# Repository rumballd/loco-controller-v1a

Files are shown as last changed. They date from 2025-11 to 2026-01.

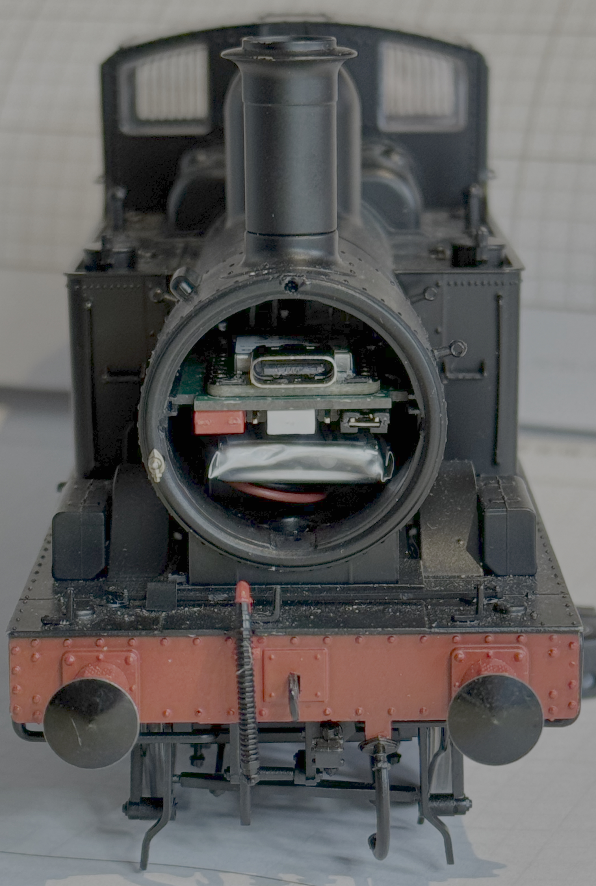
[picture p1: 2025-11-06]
docs/images/fitted_in_14XX.jpg

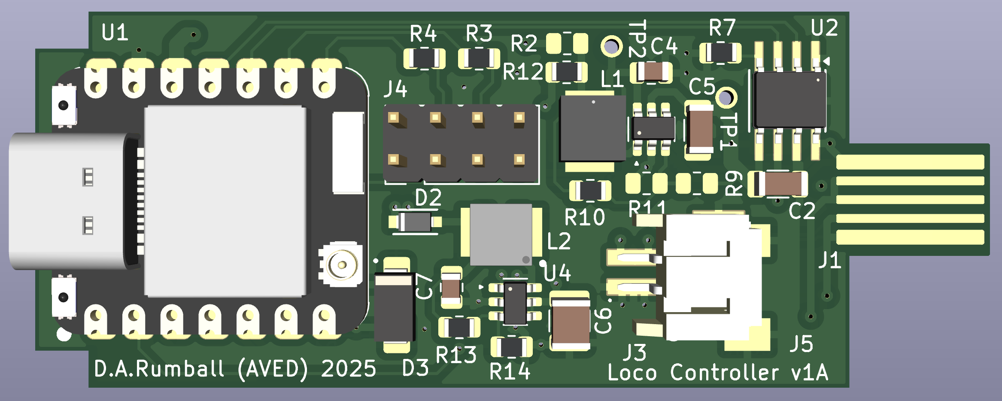
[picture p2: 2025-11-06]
docs/images/top view.png

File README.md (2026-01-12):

# loco-controller-v1a

NEW - Jan 2026, additional firmware examples and Handheld controller firmware

The Loco Controller is designed to offer a simple upgrade of Dapol and other locomotives to battery power and wireless control. It is highly integrated, incorporating an ESP32-C6 dual core MCU (microcontroller Unit) module together with a motor driver, voltage booster, battery charger and input power conditioner all on a single double sided PCB. 

The controller is designed as an exact replacement for the factory fitted DCC decoder adaptor installed in newer Dapol locomotives and installation consists of sliding out the factory PCB and replacing it with the controller. On the 58XX and B4 models the battery also slides in underneath the controller and is connected directly to the controller PCB.

For non Dapol locomotives there are a range of signals and power sources available on 2.54mm spacing pin headers including motor drive and LED outputs. In these cases though some disassembly of the locomotive body and soldering will be required.

Although designed primarily as a controller for motorised devices the device can also function as a generic wireless interface for signals, turnouts and other accessories. In such a ‘fixed’ application the unit can operate without a connected battery being powered solely by externally connected power sources and can drive multiple LED or servo outputs.

The controller implements a Wi-Fi access point and Web server that serves a page of locomotive specific controls to any standard web browser on a phone or tablet 

The initial hardware and firmware release supports:-

• Connector compatible with Dapol 0 Gauge 58XX and B4 locomotives

• Aux connector for other models with power, motor, LED and servo drive

• Integral voltage boost from VBAT to 12 V for the motor at 1 A

• Integral battery charger with power in via track or USB and 2mm JST socket for a 1S Li-Po battery

• Track power input is compatible with DCC and can be up to +-50 VDC with protection against inductive
 spikes
• Battery voltage and USB voltage can be monitored in firmware

• Links provided to isolate track power and the battery

• Charging is indicated by firebox LEDs in Dapol models and also in UI

• Multiple levels of over-current/over-voltage/over-temperature protection

• Integral Wi-Fi access point and Web server

• Control by standard Web browsers (up to four simultaneous connections)

• Firmware is updatable via USB connection

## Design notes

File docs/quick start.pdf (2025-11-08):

Loco Controller Quick Start Guide | Version 0.90 Oct 2025

### Loco Controller ‘Quick Start’ guide

Introduction

This guide gives a quick overview of choosing a battery, installation of the Loco Controller in Dapol and non Dapol models and the operation of the default firmware. There is more detail in the User Notes and other documentation.

Please read Appendix 1 of the User Notes for more information on battery care and safety.

### Battery Selection

Since the choice of battery is dependent on the particulars of the installation a battery is not provided with the unit.

The controller is designed to work only with a 1S Lithium-Polymer (Li-Po) cell with a 2 mm JST-style connector.

WARNING – Battery fire or injury. If the battery cannot supply 1 A continuous or lacks internal protection, it can overheat, ignite, or fail. Use a protected 1S Li-Po rated ≥1 A continuous from a reputable

An example of a suitable battery is the LP602248 from EEMB. (https://www.amazon.co.uk/EEMB-Battery-Rechargeable-Connector-Certified/dp/B095VVR4LB?th=1)

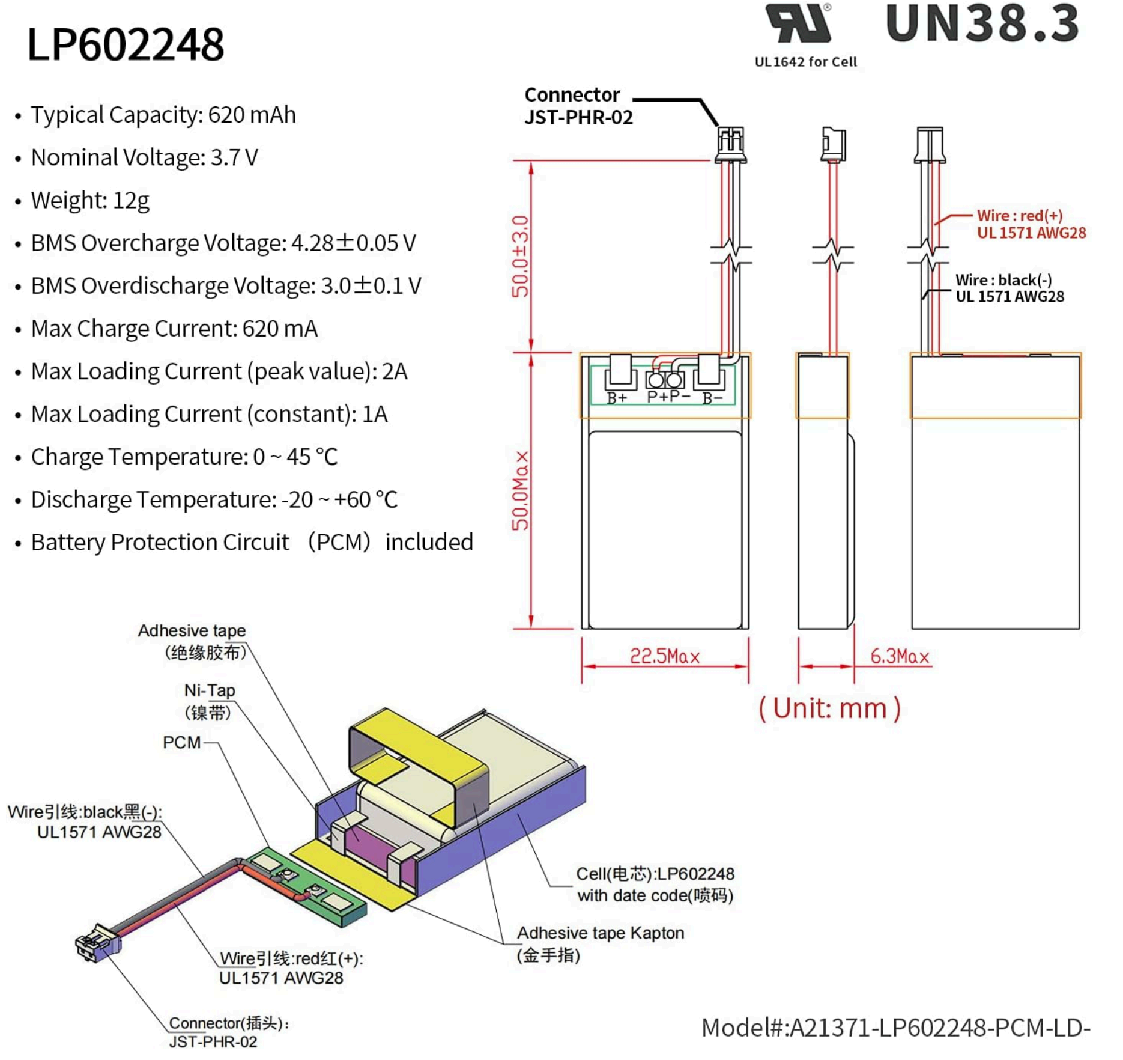
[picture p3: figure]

### Connections

The PCB has five main connectors, a USB-C socket that can be used for charging and loading firmware, the Li-Po battery connector, an ‘edge’ style connector that plugs into a Dapol locomotive’s 10 pin internal socket, a set of 2.54 mm header pins under the front of the PCB with options for powering the device and a 2.54 mm header auxiliary connector that provides access to internal power, motor, LED and servo drive in models that don’t use the Dapol connector.

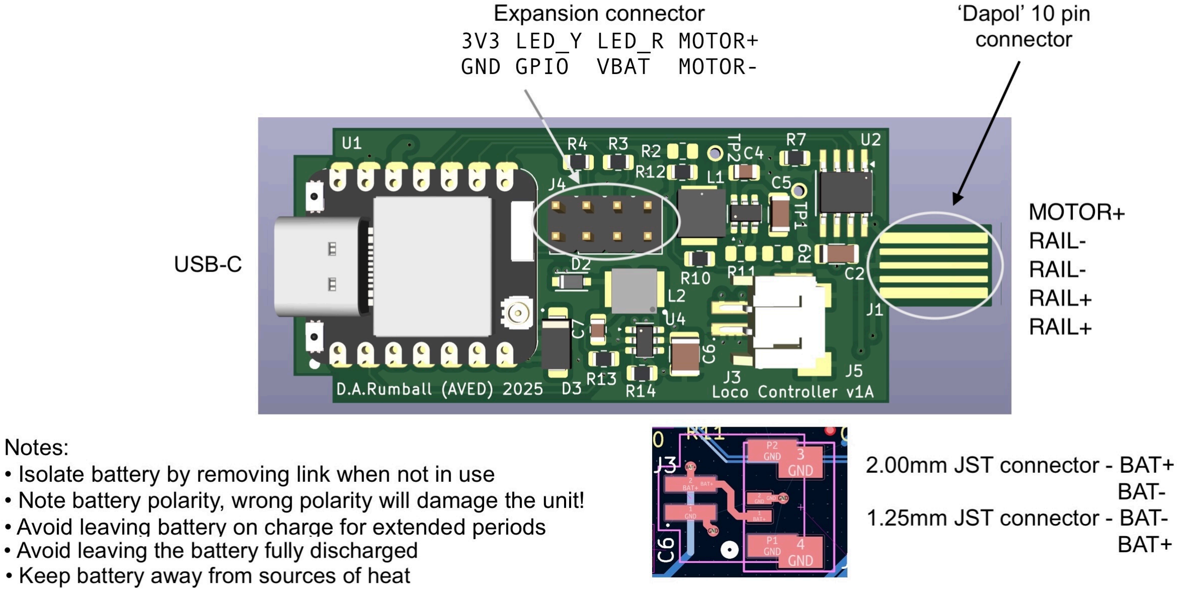
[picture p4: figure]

The battery is connected via a standard JST-style 2mm connector.

CAUTION – Equipment damage. The PCB has no reverse-polarity protection. Confirm battery polarity before you connect the battery.

The battery negative is connected to GND on the PCB and the connection diagram above shows the polarity of the battery connector.

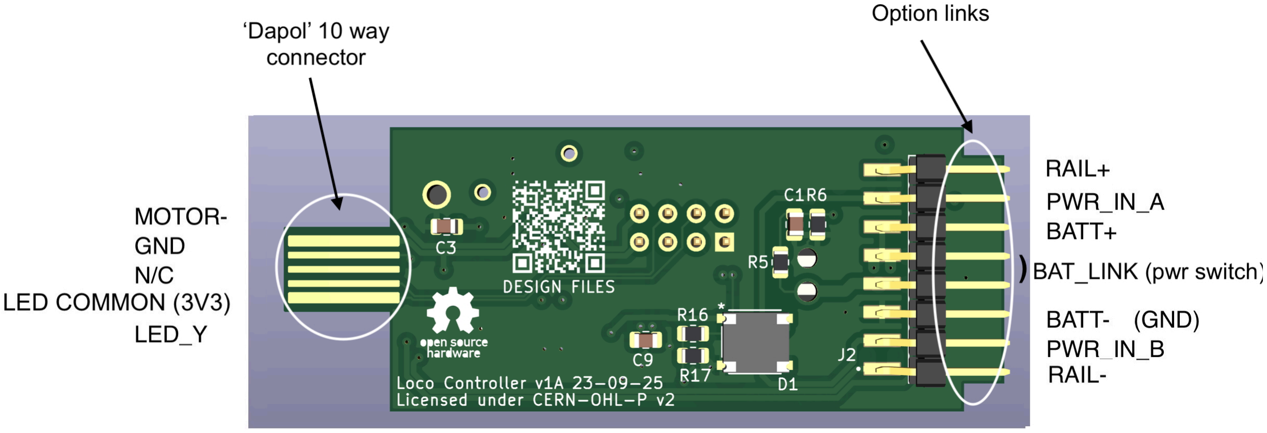
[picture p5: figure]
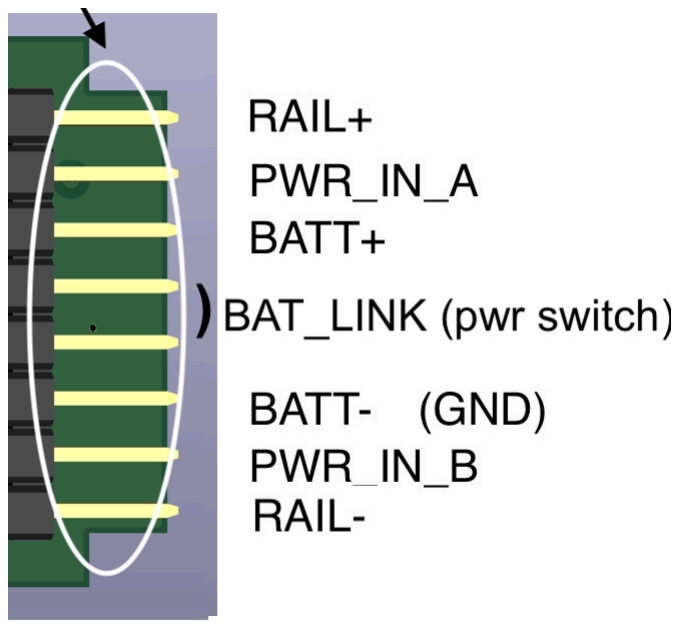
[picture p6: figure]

The links at the front of the PCB allow for the isolation of the battery which can be used as a power switch (or alternatively used for connecting an external switch) and provide for the isolation of external track power by removing the two outer links. When these links are removed the battery can still be charged via the USB-C connector and external power can be supplied through the front header pins.

### Status LEDs

There are two LEDs on the ESP32 module which are visible from the front if the smokebox door is open. Viewed from the front on the left hand side is a yellow flashing LED that indicates normal operation of the firmware and on the right hand side is a red LED that indicates charging status :-

- When no battery is connected:
- The red light turns on when the Type-C cable is connected and turns off after 30 seconds.
- When a battery is connected and the Type-C cable is plugged in for charging:
- The red light flashes.
- When the battery is fully charged via the Type-C connection:
- The red light turns off.

### Battery Charging

The controller has an on board charger which provides a maximum battery charge current of approximately 100 mA, a limit set for thermal dissipation reasons in the charger and to provide safe charging for low capacity cells. The charger is designed for Li-Po cells with high-precision linear constant-current and constant-voltage charging. It can automatically complete the processes of pre-charge, fast-charge, trickle floating charge, voltage fold-back holding, resistive voltage drop compensation and recharge. For more information please see the SGM40567 data sheet included as part of the documentation.

The supply for the charger can be either via the USB-C connector
(500 mA @ 5 V) or via the connections for external power. External power can be between 12 V and 50 VDC, is protected from inductive spikes above 54 V and is insensitive to polarity. The current draw will depend on the applied voltage. The buck regulator used in the power conditioning stage has a maximum input voltage of 70 V which is well above the TVS clipping voltage of approx 55 V.

The controller can switch seamlessly between internal battery power and external charging without operator intervention. Do not apply external power and USB power at the same time.

With the current firmware the firebox LEDs of the 58XX and B4 locomotives will illuminate if external charging power is detected providing an easy way to check on charging status from outside the locomotive. Additionally the User Interface (UI) will show a ‘charging’ indicator although note that this is an indicator of external power rather than the actual charging status. However the battery voltage can be used to estimate the actual state of charge.

### Battery Care

Please read Appendix 1 of the User Notes for more information on battery care and safety.

For long life, do not store Li-Po batteries fully charged or fully discharged. Store at about 50% state of charge (3.8 V).” Always isolate the battery after use either with an external power switch or by the battery link at the front of the PCB to avoid the Microcontroller Unit (MCU) completely draining the battery.

Although in normal operation the battery should not itself get hot, care should be taken in the location of the battery to keep it away from any heat sources. On the controller PCB these are located on the top side but as heat sinking is provided by the inner layers of the PCB the controller can become warm with use.

Care should also be taken to avoid compressing or bending the battery during installation as this will damage the cell.

Check your batteries regularly for any signs of damage, leakage or swelling of the cell. If you notice any issues then the battery should be disposed of safely. Do not dispose in your normal waste but rather take it to a recycling centre for safe disposal.

Installation in Dapol models with the internal 10 pin connector

This installation method has been tested with the current versions of the Dapol 14/58XX and B4 models which are fitted with a 10 way card edge connector. There may be other compatible models in the future but you should check that the connector pin out is the same before installation.

The installation process itself is simple. First open the smokebox door and remove the factory fitted DCC decoder carrier PCB then replace this with the loco controller and battery. Check that the PCB slides in without any force required, the battery is a loose fit and clear of the underneath of the controller PCB and the battery or it’s connecting wire aren’t fouling any parts of the locomotive. Check that the links are set as desired and the ‘alive’ yellow LED is flashing.

That’s it! You can now connect to the controller’s WiFi access point as described in the ‘Operation’ section below.

Installation in other models

As the installation in other locomotives will be varied it’s not possible to give exact instructions but instead here are some general hints and tips:-

- If not using the ‘Dapol’ connector insulate it with a wrap of tape or heat shrink.
- All the required signals and power for a typical installation should be available on the link and expansion header pins.
- ALWAYS arrange for the battery to be isolated via a power switch connected to the battery link pins.
- If there are metal parts in the vicinity of the controller it may be necessary to insulate the bottom of the PCB.
- The controller should not get hot during normal operation but air should be allowed to circulate around the PCB to remove any generated heat.
- Take great care with positioning and installation of the battery, it should not be exposed to any sources of heat or subjected to mechanical bending or pressure.

Operation

The default firmware that is shipped with the controller gives a semi realistic set of controls implementing a very simple (and not quite correct) ‘physics’ model that simulates the characteristics of a steam locomotive including momentum and friction etc.

The firmware instantiates a 2.4 GHz Wi-Fi access point capable of supporting four simultaneous connections together with a simple Web server appearing on port 80. This server provides a page defined by files stored in the ESP32’s flash based file system.

To use the controller connect your device’s Wi-Fi to the locomotives AP, which defaults to ‘LocoController’. Once connected open a browser and navigate to the IP address 192.168.4.1 then a page of controls will appear in the browser

The current interface offers three sliders
which provide a simple emulation of a steam
locomotive’s controls. To startup set the Reverser to 50% and with the brake off advance the regulator to about 33% and after a short delay the locomotive should move. The firmware implements a very simple ‘physics’ model that takes account of momentum and friction such that if the regulator is shut off the locomotive will coast, gradually slowing down. Applying the brake will increase friction thus increasing the rate of slowing. To reverse repeat the above but set the reverser to -50%

To emulate a traditional ‘direct’ controller first set the regulator to 100% after which the reverser will act as an analogue control directly
setting the locomotive speed.

As an aid to judging the charge state of the battery

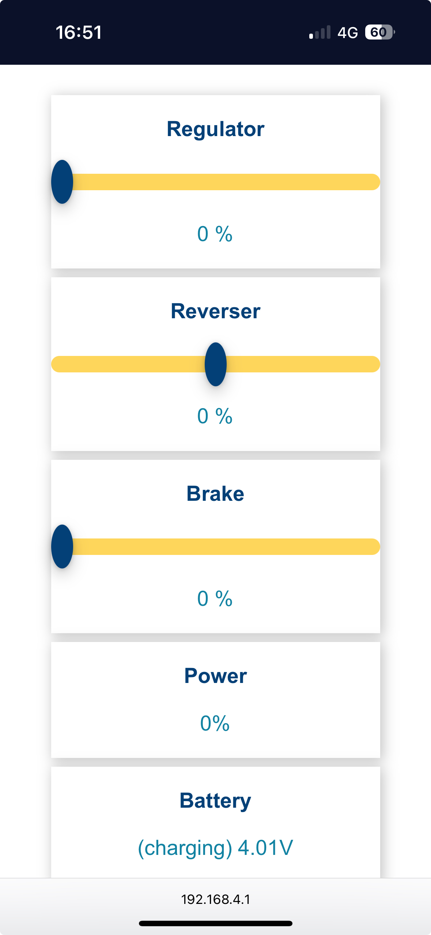
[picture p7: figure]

the battery voltage is displayed. Empty corresponds to approx 3.5 V and full 4.1 V. When track power is detected then the battery voltage will be prepended with a ‘charging’ message. Note that this is a proxy for the battery charging state as it isn’t directly possible to sense charging.

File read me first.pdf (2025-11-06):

Version 0.90 1st Oct 2025

### Loco Controller distribution 0.90 Oct 2025

This package should contain the following folders :-

* docs | - user notes, quick start and other guides.
* firmware | - Example ESP32-C6 firmware.
* hardware | - PCB fabrication files and component data sheets.

History
2025-10 | ver 0.90 | First release to the outside world.

Known Issues
None

Todo List
None

## WARNING: Please take note of the information and warnings about the use of Li-Po batteries in Appendix 1 of the

User Notes.

This project does not contain polished or shipping quality code or hardware, so use entirely at you own risk.

The project is covered under the permissive version of the CERN Open Hardware Licence Version 2 a copy of which is part of the package.

If you have any problems with the build, find any bugs, have suggestions for features and improvements etc, please email me at lococontroller@aved.org.uk

Above all, Have Fun!

David Rumball
Constantine, UK.

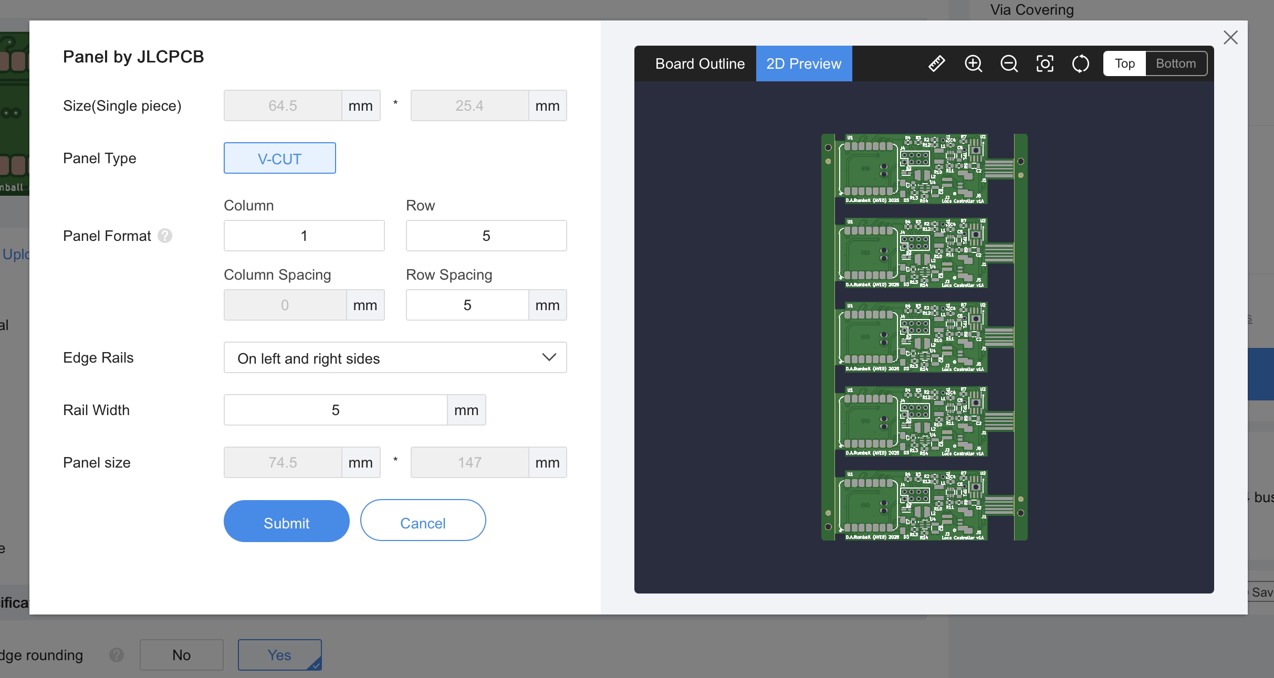
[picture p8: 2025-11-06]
hardware/PCB/fab/1x5 panel layout.jpg

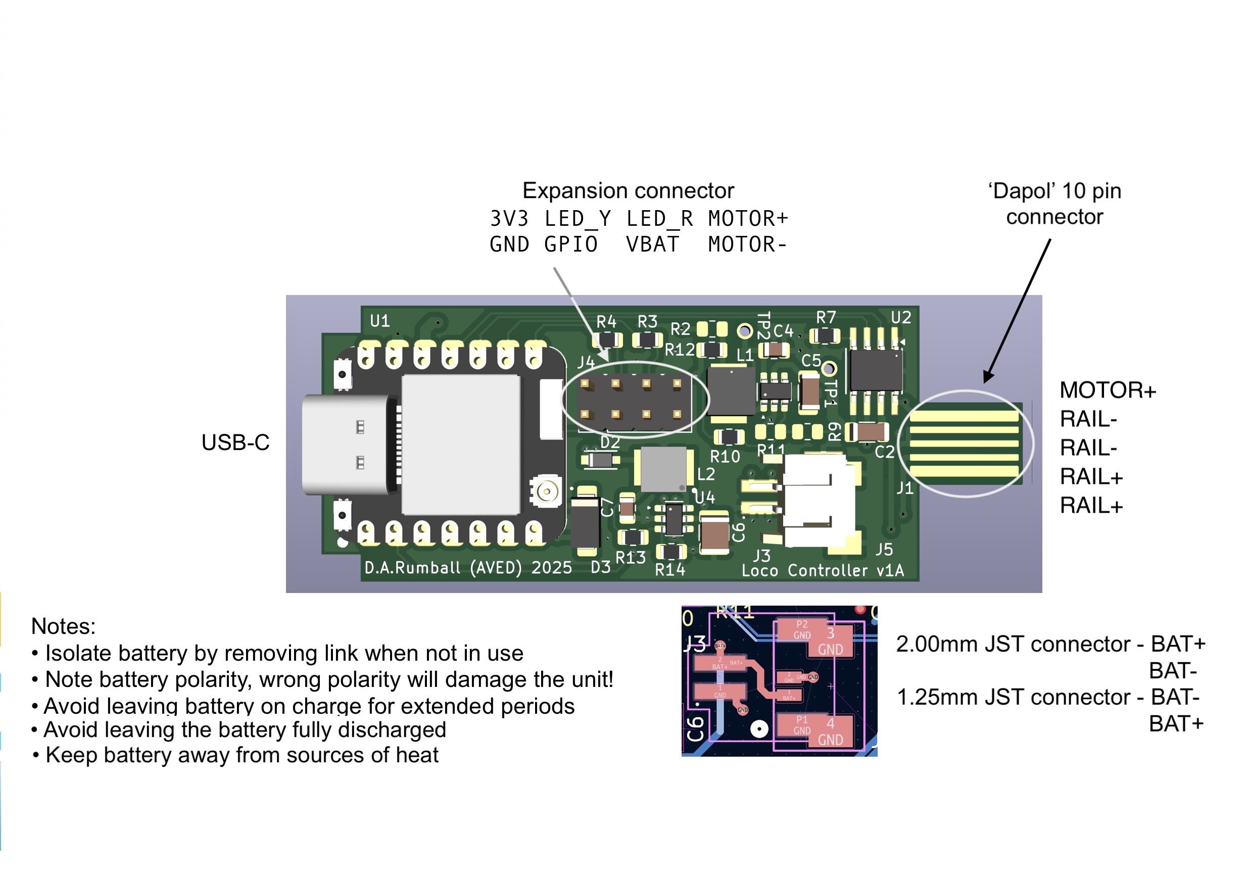
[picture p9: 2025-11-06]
docs/images/Connections - front.jpg

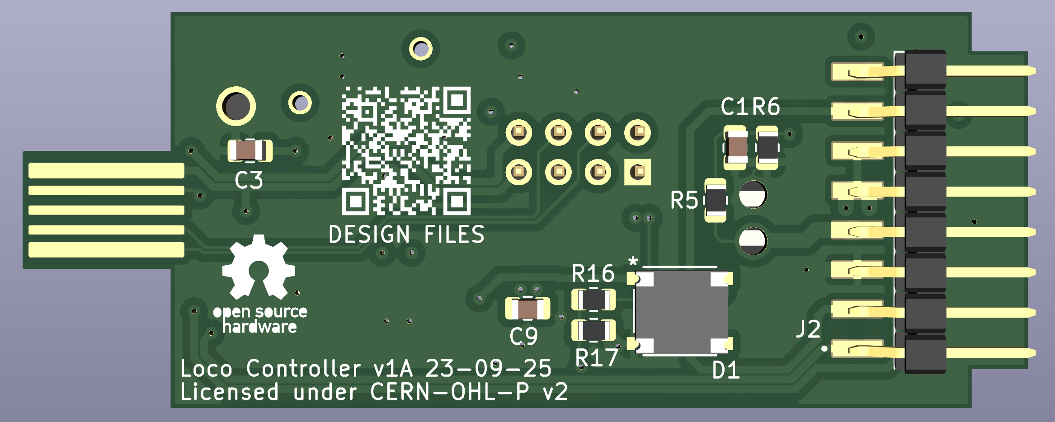
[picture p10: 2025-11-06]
docs/images/bottom view.png

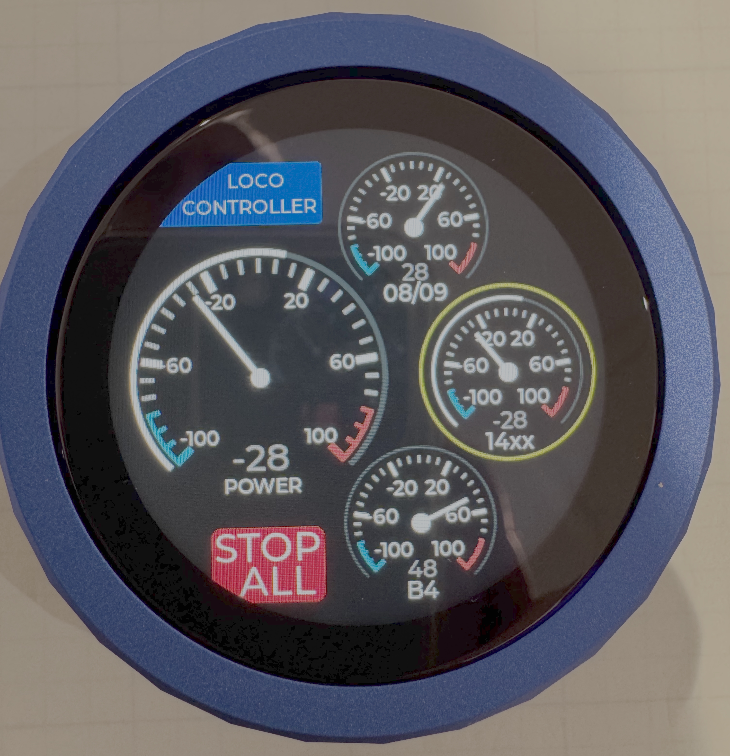
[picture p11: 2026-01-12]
docs/images/HAndheld Control UI.jpg

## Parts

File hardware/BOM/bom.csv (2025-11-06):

Designator | Footprint | Quantity | Value
C1 | C_0805 | 1 | 1uF 50V X7R ±10%
C2, C5 | C_1206 | 2 | 10uF 50V X5R ±10%
C3, C9 | C_0805 | 2 | 100nF 50V X7R ±10%
C4 | C_0805 | 1 | 25V 4.7uF X5R ±10%
C6 | C_1210 | 1 | 100V 10uF X7S ±10%
C7 | C_0805 | 1 | 10V 22uF X5R ±10%
D1 | CD-MBL2xxS_BRN | 1 | CD-MBL206SL
D2 | DIODE_MSP3V3-L | 1 | MSS1P3L-M3/89A
D3 | D_SMA | 1 | SMAJ51CA
J2 | 1X8_P2.54MM_RA | 1 | HARWIN_M20-8890845
J3 | JST_S2B-PH-SM4-TB | 1 | S2B-PH-SM4-TB
J4 | 2X4_P2.54MM_VERT | 1 | AUX CONNECTOR
L1 | SMD,4x4mm | 1 | 10U IND_ASPIAIG-S4035-100M-T_ABR
L2 | SMD,4x4mm | 1 | 15U IND_ASPIAIG-S4035-150M-T_ABR
R10, R12 | R_0805 | 2 | 0R 125mW ±1%
R13, R5, R6 | R_0805 | 3 | 100K 125mW ±1%
R14 | R_0805 | 1 | 19K6 125mW ±1%
R16 | R_0805 | 1 | 20K 125mW ±1%
R17 | R_0805 | 1 | 30K 125mW ±1%
R3, R4 | R_0805 | 2 | 330R 125mW ±1%
R7 | R_0805 | 1 | 68K 125mW ±1%
U1 | XIAO-ESP32C6-SMD | 1 | XIAO-ESP32-C6
U2 | HTSOP-8 | 1 | DRV8871DDAR
U3 | SOT-23-6 | 1 | TLV61046ADB
U4 | SOT-23-6 | 1 | LMR51606YDBVR

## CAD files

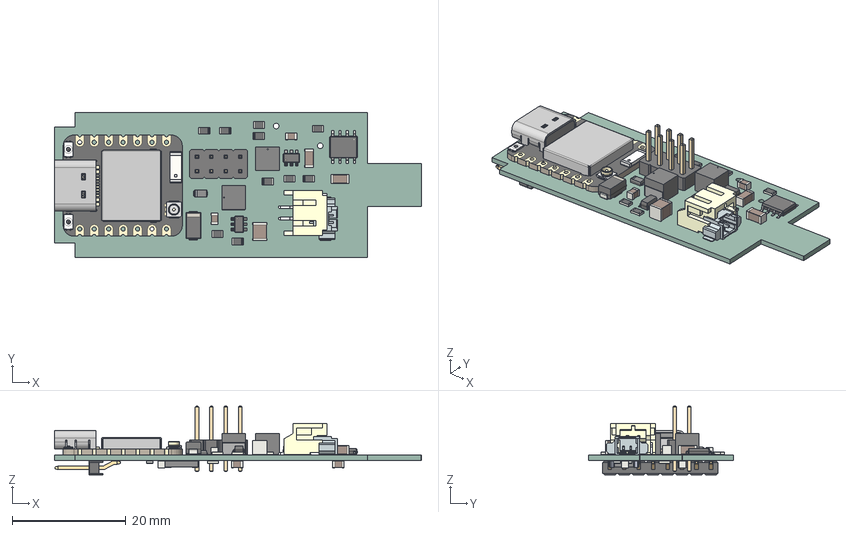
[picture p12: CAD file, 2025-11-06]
hardware/PCB/3D/loco_decoder_v1a.step
64.5 x 25.4 x 12.1 mm
R_0805_2012Metric x 14
SOT-23-6 x 2
kicad_embedded_4268D40089215B1AC33364D5905491C9 x 2
BOSS-EXTRUDE14_8_
BOSS-EXTRUDE7_4_
BOSS-EXTRUDE7_3_
BOSS-EXTRUDE14_4_
BOSS-EXTRUDE14_2_
BOSS-EXTRUDE14_11_
BOSS-EXTRUDE7_7_
BOSS-EXTRUDE14_9_
BOSS-EXTRUDE14_3_
BOSS-EXTRUDE14_7_
MIRROR2
BOSS-EXTRUDE14_5_
BOSS-EXTRUDE14_12_
BOSS-EXTRUDE7_8_
BOSS-EXTRUDE7_1_
BOSS-EXTRUDE14_10_
BOSS-EXTRUDE7_9_
BOSS-EXTRUDE14_6_
BOSS-EXTRUDE14_1_
BOSS-EXTRUDE7_6_
BOSS-EXTRUDE7_2_
CUT-EXTRUDE5
BOSS-EXTRUDE7_5_
U.FL Connector v1
Shield
SKTAAAE010 v1 x 2
KH5220-A36 (Ceramic Antenna) v2
Texas_HTSOP-8-1EP_3.9x4.9mm_P1.27mm_EP2.85x4.9mm_Mask2.4x3.1mm_ ThermalVias
C_1210_3225Metric
D_SMA
C_1206_3216Metric x 2
C_0805_2012Metric x 5
PinHeader_2x04_P2.54mm_Vertical
terminals
logo
kicad_embedded_1D2A0216B19EBB82418A5B4AF2BA824B
kicad_embedded_DDCFF2373EAE1CF9C5861DB1AABFC711
kicad_embedded_CD2B932B5F435B6E3418D692FA3D0E84
loco-decoder-v1a_PCB

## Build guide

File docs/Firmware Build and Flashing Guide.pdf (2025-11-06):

Firmware Build and Flashing Guide | Version 0.90 1st Oct 2025

Loco Controller Firmware Build and Flashing Guide

Introduction

The Loco Controller is designed to be simple to upgrade to encourage experimentation and modification of its firmware and so the firmware is based around the popular and Arduino framework. In order to be able to modify the supplied examples and download to the hardware it’s necessary to install the free and cross-platform Arduino IDE. (https://docs.arduino.cc/software/ide-v2/tutorials/getting-started-ide-v2/)

Prerequisites

MacOS - Version 10.15: "Catalina" or newer, 64 bits Linux - 64 bit
Windows - Win 10 and newer, 64 bit

Step by step guide

The guide below is a quick walkthrough of installing the IDE and building and flashing the LocoController’s firmware. For more detail see the Random Nerd guide 'Installing an ESP32 Board in Arduino IDE 2 (Windows, Mac OS X, Linux)' (https://randomnerdtutorials.com/installing-esp32-arduino-ide-2-0/) and Seeed Studio’s Wiki on the ESP32C6. (https://wiki.seeedstudio.com/xiao_esp32c6_getting_started/#software-preparation) Some of the examples require that the ESP32C6’s flash based file system se set up for more details on this see Random Nerd’s guide ‘Install ESP32 LittleFS Uploader (Upload Files to the Filesystem)’ (https://randomnerdtutorials.com/arduino-ide-2-install-esp32-littlefs/)

Step 1 - Install the Arduino IDE 2

Before proceeding make sure you have the Arduino IDE 2 (https://docs.arduino.cc/software/ide-v2/tutorials/getting-started-ide-v2/) installed on your computer, this can be obtained from the Arduino download page. (https://www.arduino.cc/en/software/) The IDE is cross-platform and will work with MacOS, Linux and Windows and detailed install instructions for each OS can be found here. (https://docs.arduino.cc/software/ide-v2/tutorials/getting-started/ide-v2-downloading-and-installing/) The examples are tested with version 2.3.6.

Step 2 - Install the ESP32 Add-on

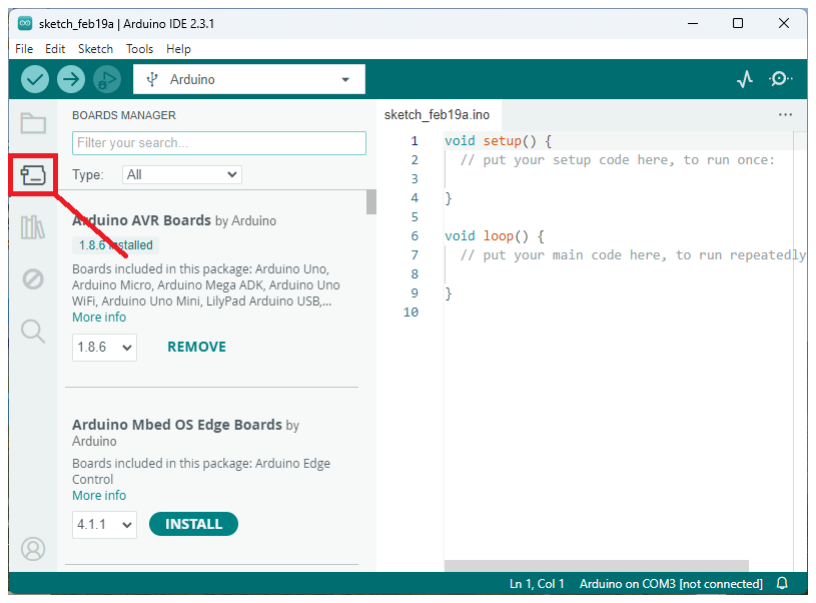
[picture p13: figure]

Once the IDE is installed the next step is add the ESP32 board packages. Open the Boards Manager by navigating to Tools > Board > Boards Manager… or simply click the Boards Manager icon in the LH sidebar.

In the search box type ‘ESP32’ and hit the install button for the package ‘esp32 by Espressif Systems’ The install should only take a few seconds, when it’s finished close and reopen the IDE.

Step 3 - Select the XIAO ESP32C6 board

Before the sketch can be
compiled the IDE needs to know
the type and serial port of the attached board. In the drop down list at the top of the IDE window choose ‘Select other board and port…’, search for ‘XIAO’ and select ‘ESP32C6’. To the Right Hand Side (RHS) of
this dialog will be a list of
attached serial devices, one of

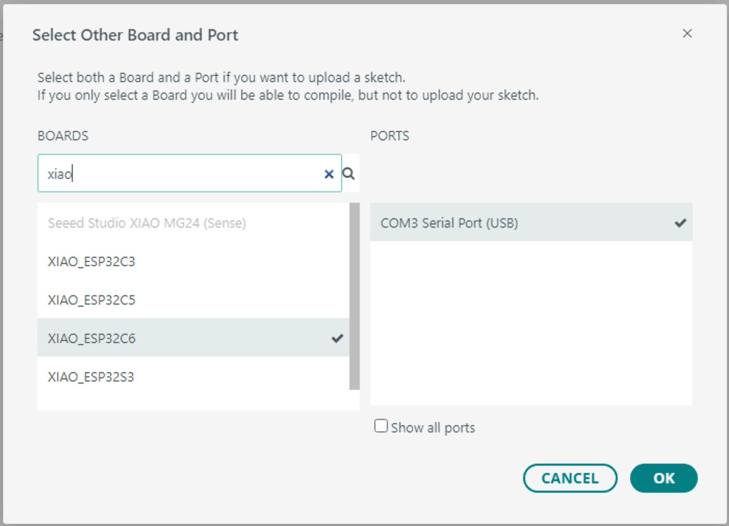
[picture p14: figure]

which will be the Loco Controller. A simple way to determine the correct port is to disconnect the unit and see which entry disappears. Reconnect the board and then select its entry in the list.

Step 4 - Add the Required Libraries

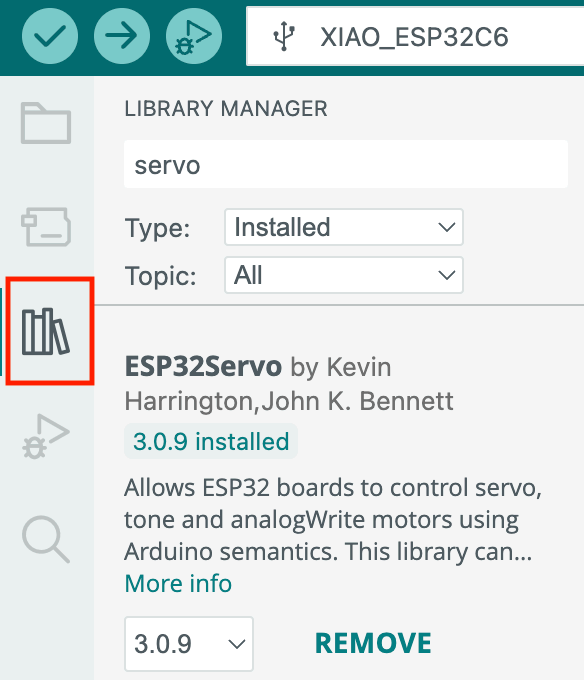
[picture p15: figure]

In order to compile the example sketches additional libraries are required to be installed. Open the Library Manager by navigating to Tools > Manage Libraries… or simply click the Library Manager icon in the left side bar.
Open the Boards Manager by navigating to Tools > Board > Boards Manager… or simply click the Boards Manager icon in the LH sidebar.

Search for and add the following libraries:-

Async TCP (3.4.9) by ESP32 Async TCP

ESP Async WebServer (3.8.1) by ESP32Async

Arduino_JSON (0.2.0) by Arduino

EmbAJAX (0.2.0) by Thomas Friedrichsmeier

Step 5 - Install the LittleFS Uploader

The default example stores html and other files in its onboard flash filesystem (LittleFS). This uses a LittleFS upload plugin (https://github.com/earlephilhower/arduino-littlefs-upload) which needs to be installed separately. The instructions for this vary with OS so and Random Nerd has a good description of the process at ‘Install ESP32 LittleFS Uploader (Upload Files to the Filesystem)’. (https://randomnerdtutorials.com/arduino-ide-2-install-esp32-littlefs/)

Restart the IDE at this point to ensure all the above changes are registered.

Step 6 - Load and Compile an Example Sketch

There are several example sketches in the distribution located in the ‘firmware’ folder. Each sketch has the extension .ino and opening this file will load the sketch into the IDE. Any modifications made can be tested with the ‘Verify’ button in the top bar.

Step 7 - Download to the Hardware

Check that the correct board and serial port are selected, search for ‘XIAO_ESP32C6’ and select this board. To the RHS of this dialog will be a list of attached serial devices, use the port identified in step 3. Reconnect the board and then select its entry in the list.

Once the board is selected close the
dialog and hit the ‘upload’ button (right facing
arrow). The firmware will compile and begin to

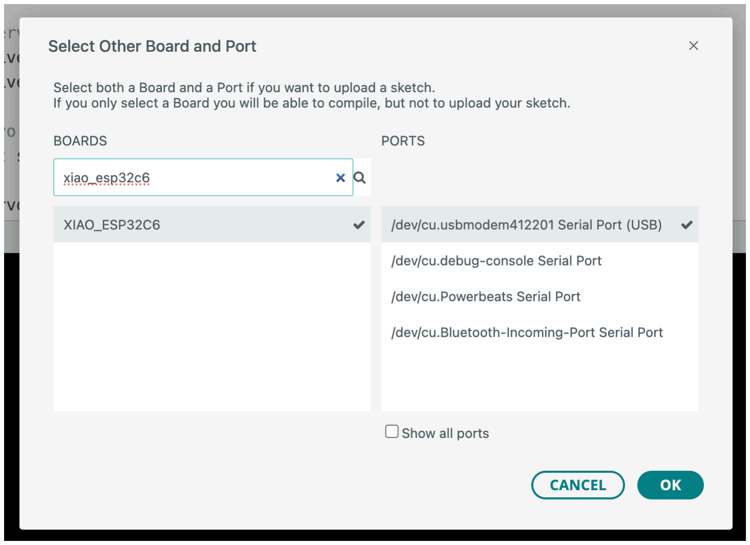
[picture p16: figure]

download to the device ending with the message ‘Hard resetting via RTS pin…’.

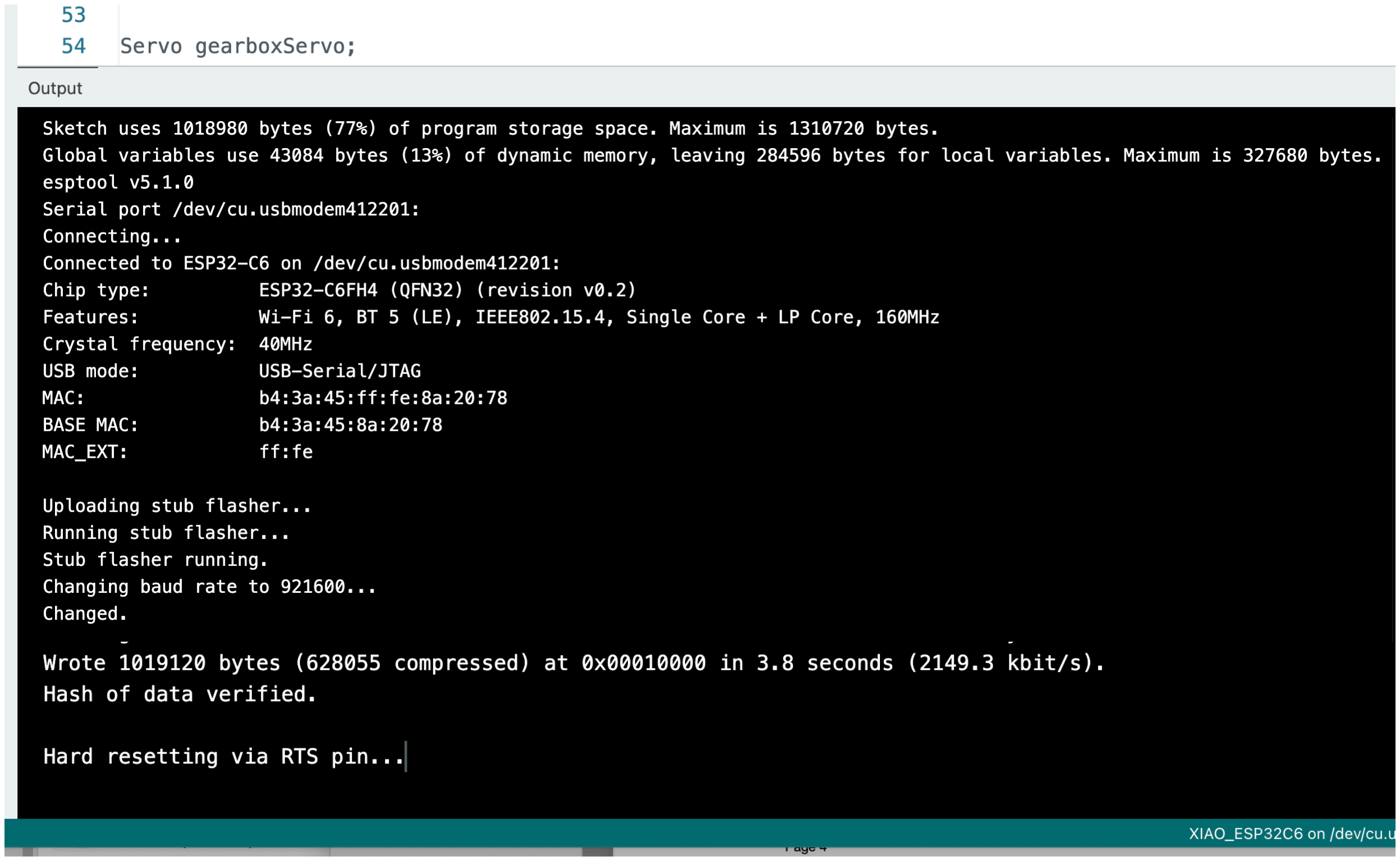
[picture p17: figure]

The example sketches will flash the ‘it’s alive’ yellow LED next to the USB-C connector indicating that the firmware has downloaded correctly and is running.

Some examples require loading files into the LittleFS filesystem which is part of the onboard flash memory. These reside in a folder named ‘data’ inside the same folder as the sketch and only need to be loaded before the first load of the sketch or whenever the files are changed.

To upload the files to the Loco Controller check that the serial monitor is closed (icon on the Right hand end of the top bar) then hold ‘⌘’ + ‘shift’ + ‘P’ on MacOS or ‘ctrl’ + ‘shift’ + ‘P’ on Windows to open the command line, search for ‘littleFS’ and select ‘LittleFS to Pico/ESP8266/ESP32’. The command takes a few seconds and ends with the message ‘completed upload’. If the upload fails with the error message ‘ERROR: No port specified, check IDE menus’ restart the IDE and try again.

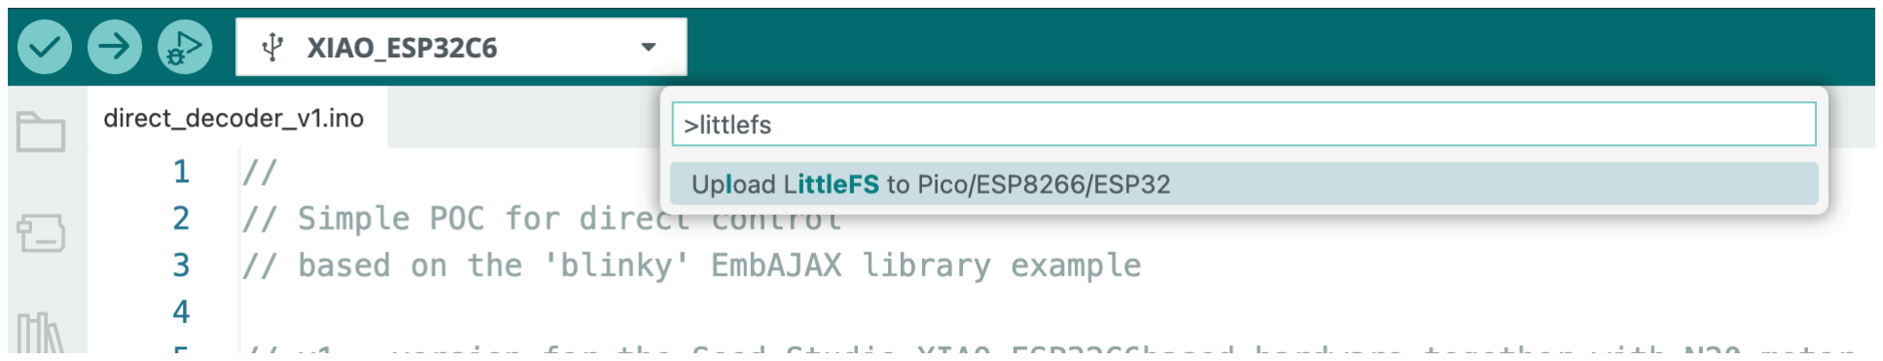
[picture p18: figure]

Download Troubleshooting

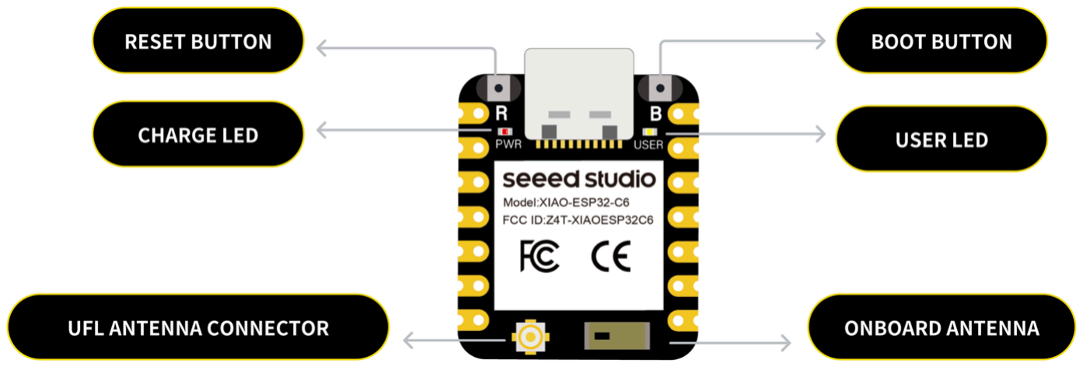
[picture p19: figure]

If the ESP32C6’s bootloader is inactive the IDE won’t be able to connect to the device during flashing. If this happens press and hold the ‘BOOT’ button on the ESP32C6 module whilst applying power, then release. The ‘BOOT’ button is located next to the USB-C connector opposite pin 1.

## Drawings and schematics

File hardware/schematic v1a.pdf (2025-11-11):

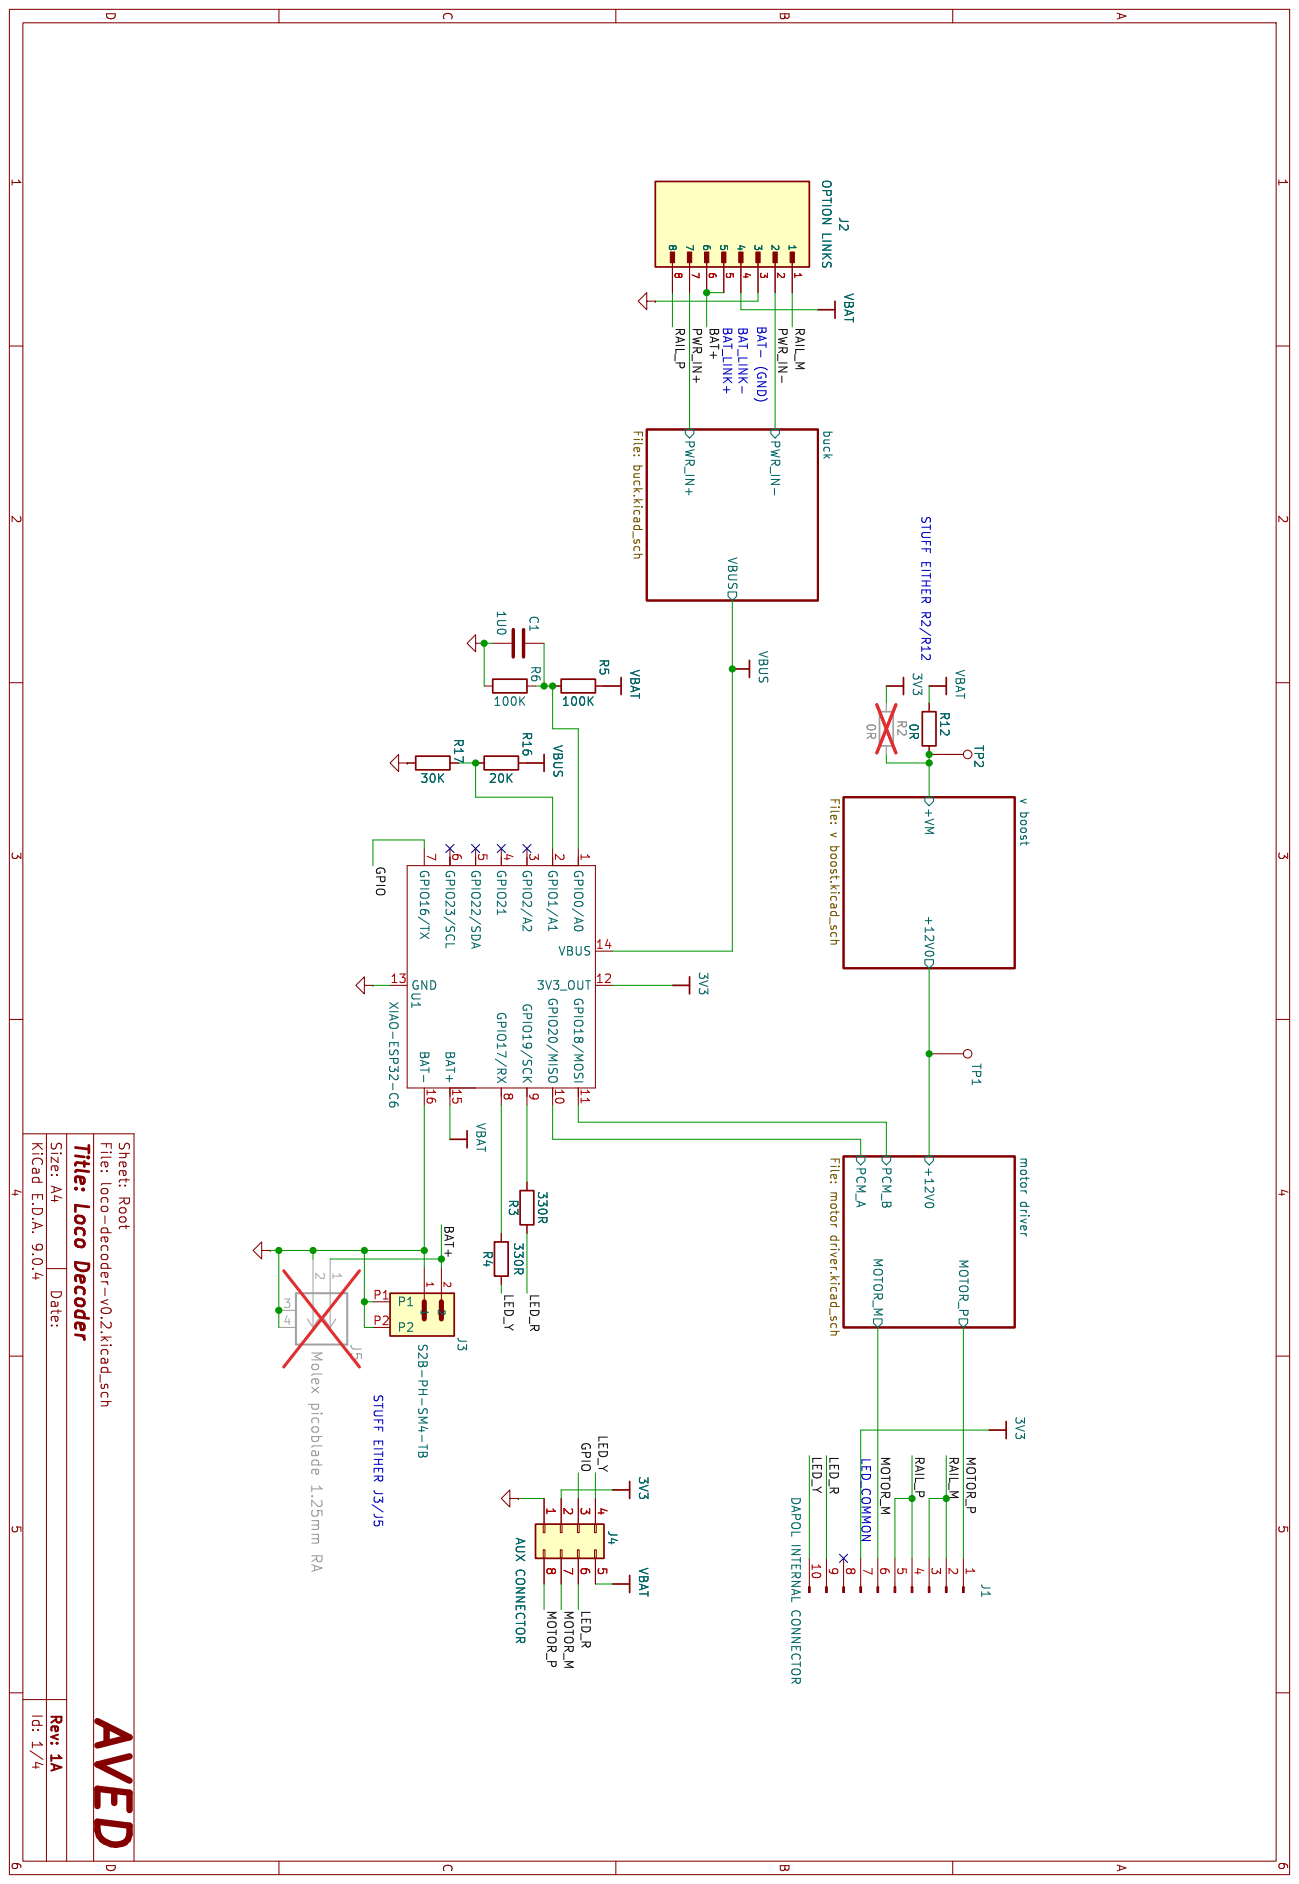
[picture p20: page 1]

BAT_LINK+ BAT_LINK- STUFF EITHER R2/R12 BAT- (GND) LED_COMMON

PCM_B motor driver File: motor driver.kicad_sch +12V0 +VM

7 VBUS 14 3V3_OUT 12 GND 13 GPIO18/MOSI 11 GPIO20/MISO

Date: KiCad E.D.A. 9.0.4 Rev: 1A Size: A4

Id: 1/4 Title: Loco Decoder File: loco-decoder-v0.2.kicad_sch Sheet: Root AVED

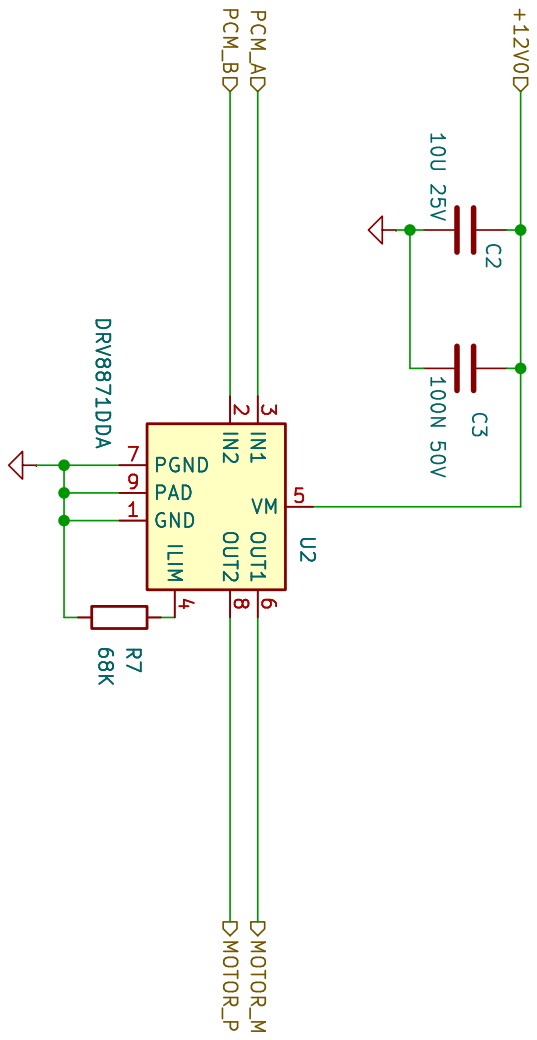
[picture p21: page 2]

Date: KiCad E.D.A. 9.0.4 Rev: 1A Size: A4

Id: 2/4 Title: Loco Decoder File: motor driver.kicad_sch Sheet: motor driver AVED

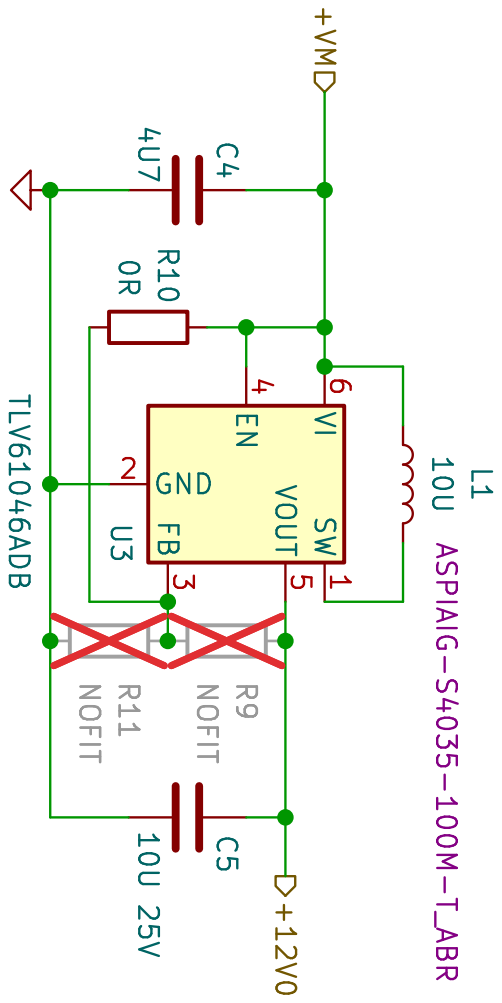
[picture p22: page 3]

Date: KiCad E.D.A. 9.0.4 Rev: 1A Size: A4

Id: 3/4 Title: Loco Decoder File: v boost.kicad_sch Sheet: v boost AVED

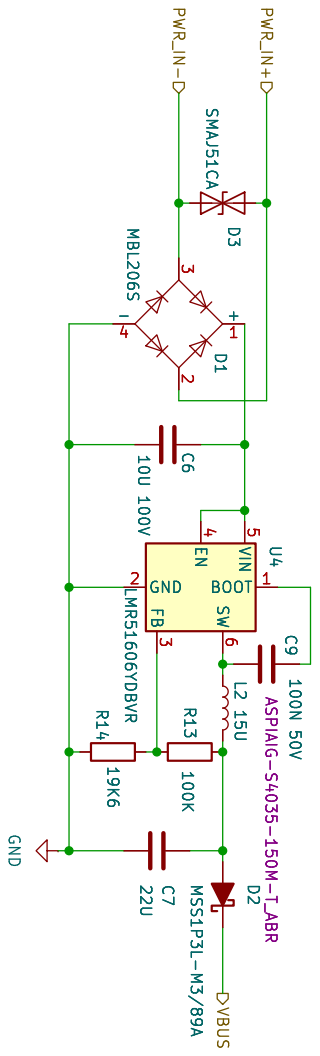
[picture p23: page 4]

Date: KiCad E.D.A. 9.0.4 Rev: 1A Size: A4

Id: 4/4 Title: Loco Decoder File: buck.kicad_sch Sheet: buck AVED

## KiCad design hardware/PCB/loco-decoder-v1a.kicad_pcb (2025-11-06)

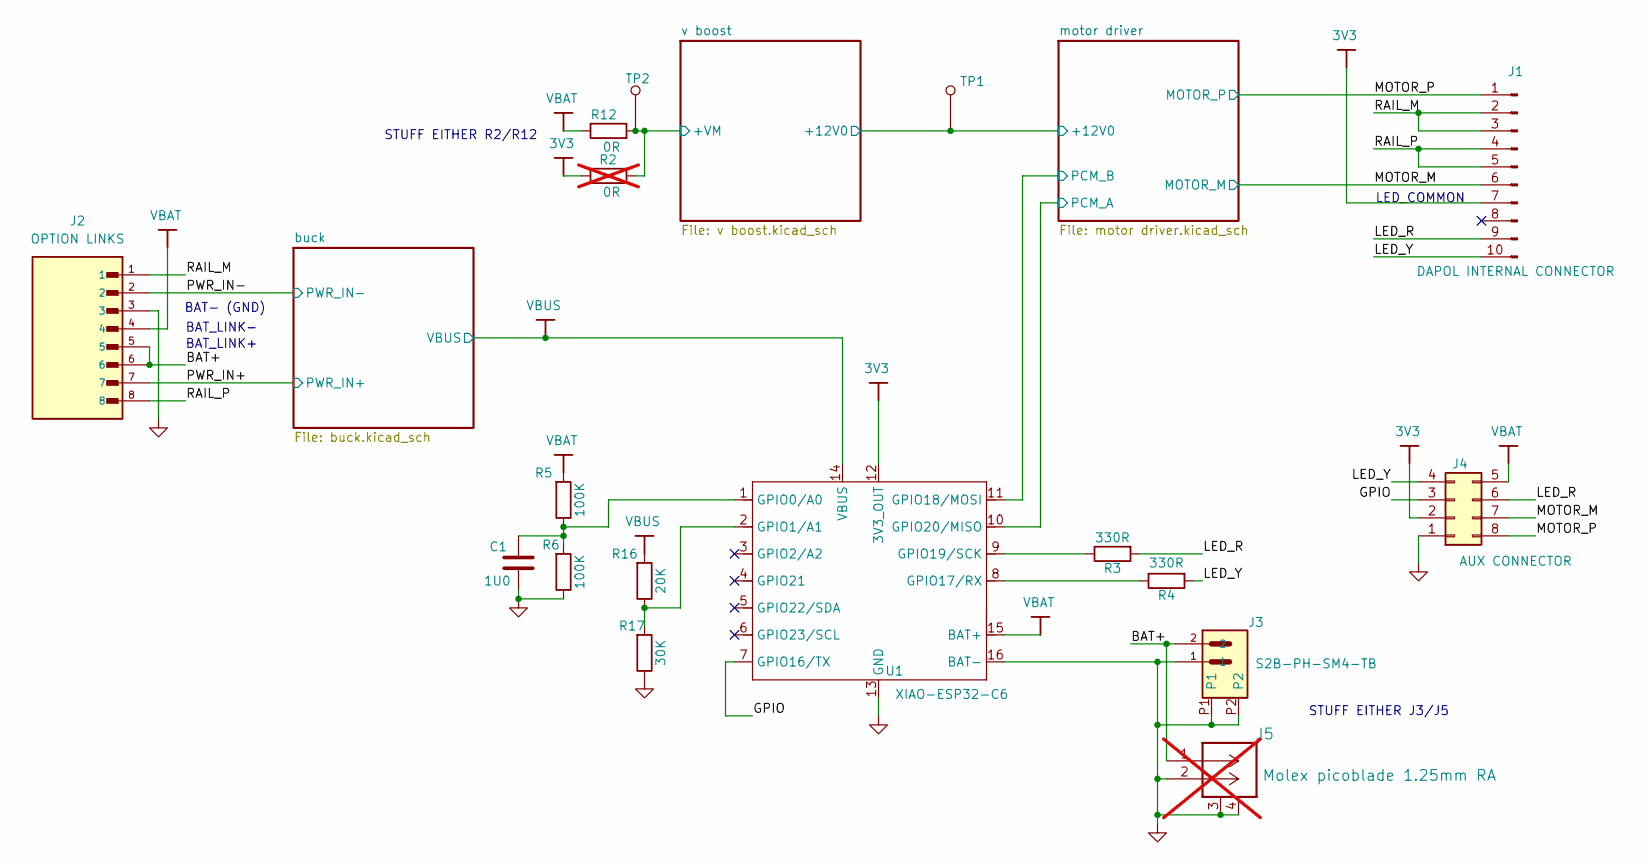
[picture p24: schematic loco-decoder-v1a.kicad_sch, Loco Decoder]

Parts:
C1: 1U0; C_0805_2012Metric
J1: DAPOL INTERNAL CONNECTOR; EDAC 302 SERIES CARD EDGE CONNECTOR 10way 2 row
J2: OPTION LINKS; HARWIN_M20-8890845
J3: S2B-PH-SM4-TB; JST_S2B-PH-SM4-TB
J4: AUX CONNECTOR; PinHeader_2x04_P2.54mm_Vertical
J5: Molex picoblade 1.25mm RA; CONN_532610001-SD_02_MOL; not fitted
R2: 0R; R_0805_2012Metric; not fitted
R3, R4: 330R; R_0805_2012Metric
R5, R6: 100K; R_0805_2012Metric
R12: 0R; R_0805_2012Metric
R16: 20K; R_0805_2012Metric
R17: 30K; R_0805_2012Metric
TP1, TP2: 3_Through hole test point; Test Point 1mm
U1: XIAO-ESP32-C6; XIAO-ESP32C6-SMD

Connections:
3V3: J1.7, J4.2, R2.1, U1.12 (3V3_OUT)
/BAT+: J2.5, J2.6, J3.2, J5.1
/GPIO: J4.3, U1.7 (GPIO16/TX)
/LED_R: J1.9, J4.6, R3.2
/LED_Y: J1.10, J4.4, R4.2
/MOTOR_M: J1.6, J4.7; also elsewhere on the board
/MOTOR_P: J1.1, J4.8; also elsewhere on the board
/PWR_IN+: J2.7; also elsewhere on the board
/PWR_IN-: J2.2; also elsewhere on the board
/RAIL_M: J1.2, J1.3, J2.1
/RAIL_P: J1.4, J1.5, J2.8
/motor driver/+12V0: TP1.1; also elsewhere on the board
/motor driver/PCM_A: U1.10 (GPIO20/MISO); also elsewhere on the board
/motor driver/PCM_B: U1.11 (GPIO18/MOSI); also elsewhere on the board
/v boost/+VM: R2.2, R12.2, TP2.1; also elsewhere on the board
GND: C1.2, J2.3, J3.1, J3.P1, J3.P2, J4.1, J5.2, J5.3, J5.4, R6.1, R17.1, U1.13 (GND), U1.16 (BAT-); also elsewhere on the board
unnamed: C1.1, R5.1, R6.2, U1.1 (GPIO0/A0)
unnamed: R16.1, R17.2, U1.2 (GPIO1/A1)
unnamed: R4.1, U1.8 (GPIO17/RX)
unnamed: R3.1, U1.9 (GPIO19/SCK)
VBAT: J2.4, J4.5, R5.2, R12.1, U1.15 (BAT+)
VBUS: R16.2, U1.14 (VBUS); also elsewhere on the board

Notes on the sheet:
STUFF EITHER R2/R12
STUFF EITHER J3/J5
LED_COMMON
BAT- (GND)
BAT_LINK-
BAT_LINK+

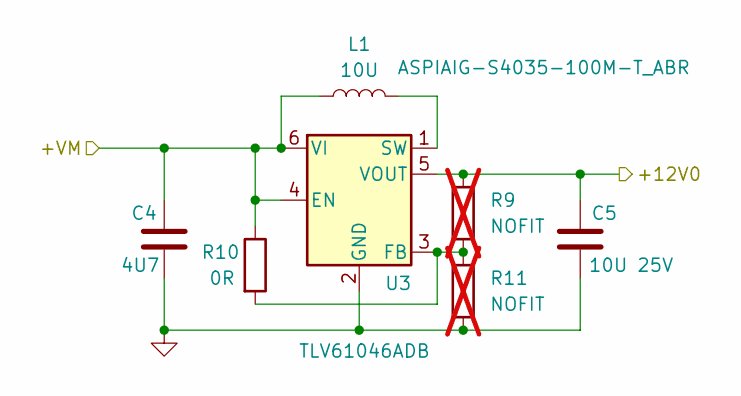
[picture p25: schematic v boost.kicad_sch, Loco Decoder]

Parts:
C4: 4U7; C_0805_2012Metric
C5: 10U 25V; C_1206_3216Metric
L1: 10U; IND_ASPIAIG-S4035-100M-T_ABR
R9, R11: NOFIT; R_0805_2012Metric; not fitted
R10: 0R; R_0805_2012Metric
U3: TLV61046ADB; SOT-23-6

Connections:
/motor driver/+12V0: C5.1, R9.1, U3.5 (VOUT); also elsewhere on the board
/v boost/+VM: C4.1, L1.1, R10.1, U3.4 (EN), U3.6 (VI); also elsewhere on the board
GND: C4.2, C5.2, R11.2, U3.2 (GND); also elsewhere on the board
unnamed: R9.2, R10.2, R11.1, U3.3 (FB)
unnamed: L1.2, U3.1 (SW)

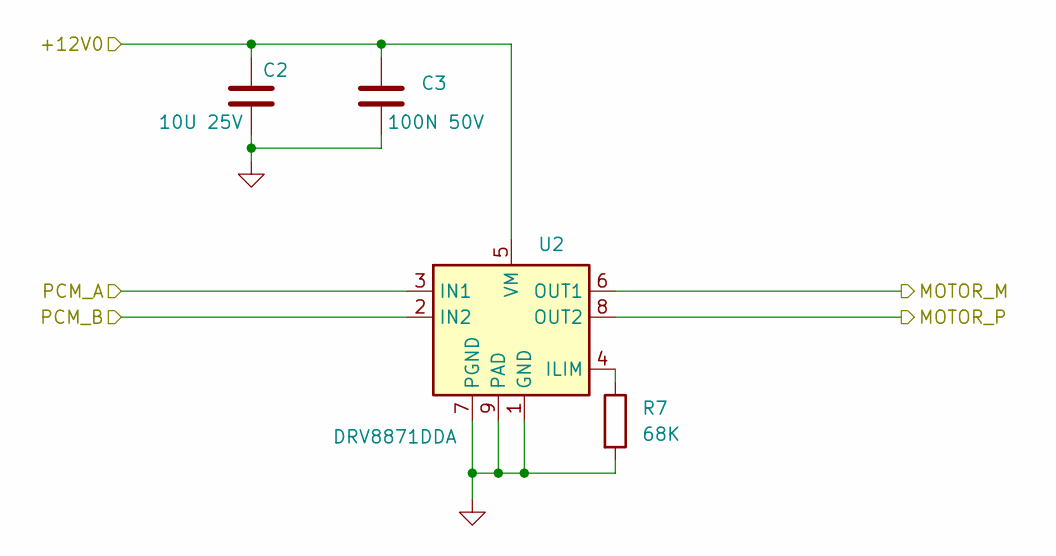
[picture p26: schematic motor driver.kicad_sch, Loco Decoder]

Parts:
C2: 10U 25V; C_1206_3216Metric
C3: 100N 50V; C_0805_2012Metric
R7: 68K; R_0805_2012Metric
U2: DRV8871DDA; Texas_HTSOP-8-1EP_3.9x4.9mm_P1.27mm_EP2.95x4.9mm_Mask2.4x3.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

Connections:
/MOTOR_M: U2.6 (OUT1); also elsewhere on the board
/MOTOR_P: U2.8 (OUT2); also elsewhere on the board
/motor driver/+12V0: C2.1, C3.1, U2.5 (VM); also elsewhere on the board
/motor driver/PCM_A: U2.3 (IN1); also elsewhere on the board
/motor driver/PCM_B: U2.2 (IN2); also elsewhere on the board
GND: C2.2, C3.2, R7.2, U2.1 (GND), U2.7 (PGND), U2.9 (PAD); also elsewhere on the board
unnamed: R7.1, U2.4 (ILIM)

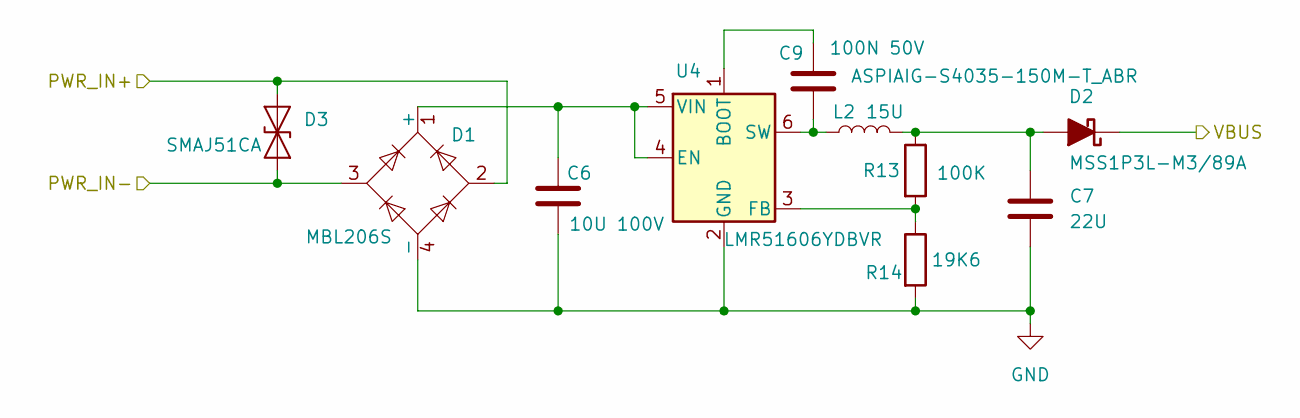
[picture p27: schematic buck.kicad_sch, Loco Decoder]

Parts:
C6: 10U 100V; C_1210_3225Metric
C7: 22U; C_0805_2012Metric
C9: 100N 50V; C_0805_2012Metric
D1: MBL206S; CD-MBL2xxS_BRN
D2: MSS1P3L-M3/89A; DIODE_MSP3V3-L
D3: SMAJ51CA; D_SMA
L2: 15U; WE-MAPI_4020
R13: 100K; R_0805_2012Metric
R14: 19K6; R_0805_2012Metric
U4: LMR51606YDBVR; SOT-23-6

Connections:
/PWR_IN+: D1.2, D3.1 (A1); also elsewhere on the board
/PWR_IN-: D1.3, D3.2 (A2); also elsewhere on the board
GND: C6.2, C7.2, D1.4 (-), R14.2, U4.2 (GND); also elsewhere on the board
unnamed: C6.1, D1.1 (+), U4.4 (EN), U4.5 (VIN)
unnamed: C7.1, D2.1 (A), L2.2, R13.1
unnamed: C9.1, U4.1 (BOOT)
unnamed: R13.2, R14.1, U4.3 (FB)
unnamed: C9.2, L2.1, U4.6 (SW)
VBUS: D2.2 (K); also elsewhere on the board

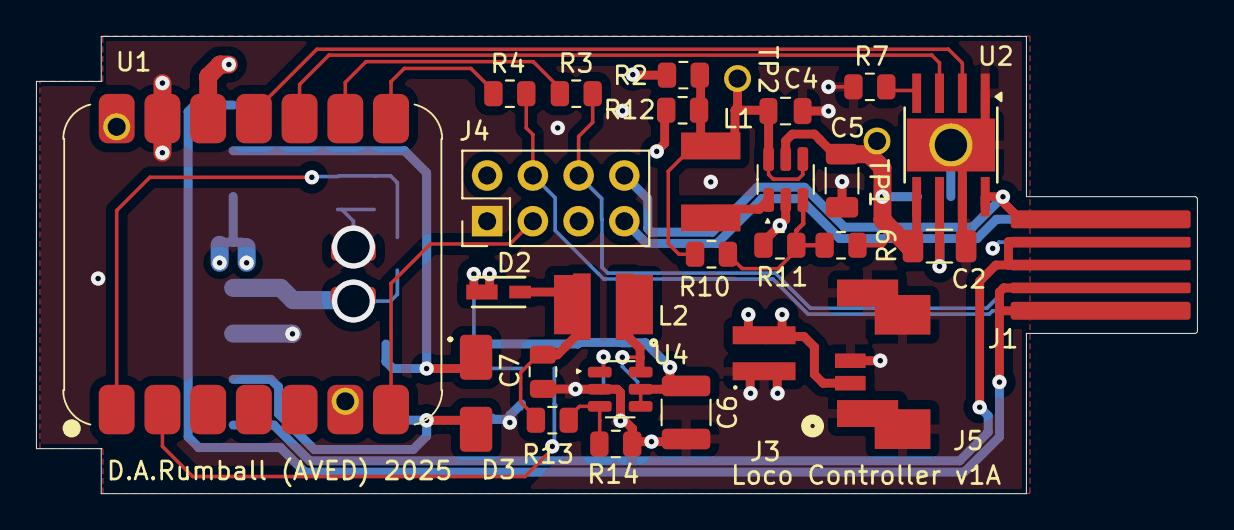
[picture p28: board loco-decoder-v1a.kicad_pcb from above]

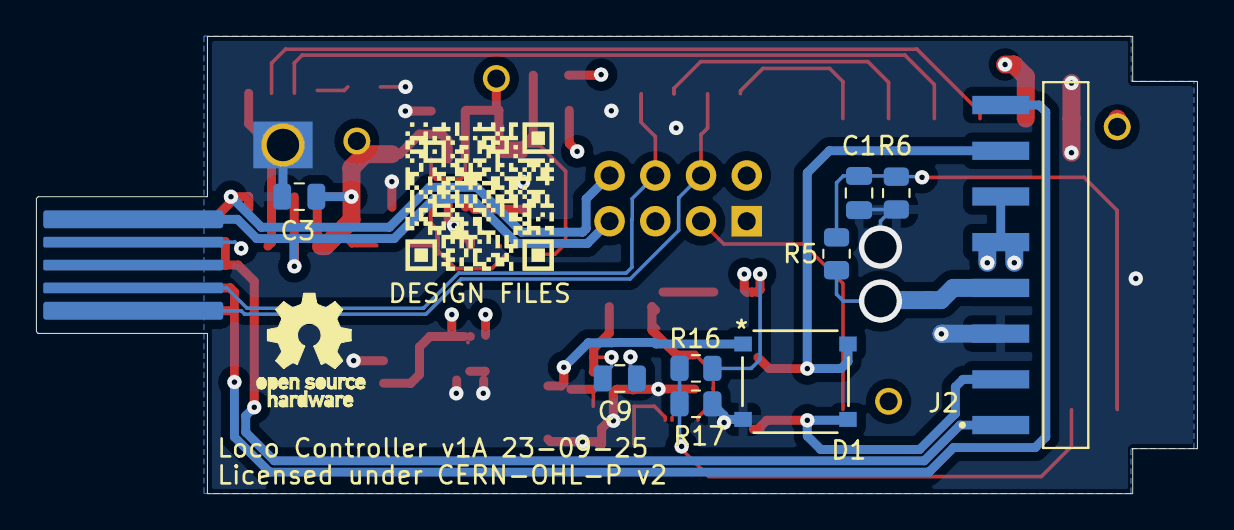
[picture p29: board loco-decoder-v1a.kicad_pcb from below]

Board: 4 copper layers, 64.5 x 25.4 mm, 41 parts (9 on the bottom side), 30 nets.

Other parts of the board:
DESIGN: DESIGN FILES; DESIGN FILES QR CODE
FD1, FD2: 3_Through hole test point; Test Point 1mm

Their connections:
VBUS: FD1.1; also elsewhere on the board

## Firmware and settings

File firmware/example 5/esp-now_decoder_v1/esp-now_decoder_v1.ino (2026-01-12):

//
// Simple POC for control of locomotive usung the ESP-NOW protocol
// based on target example by VolosR 
// github.com/VolosR/Knob18Meters/tree/main/KnobRGBControl
// 

// v1 - initial version

#include <Arduino.h>
#include <WiFi.h>
#include <esp_now.h>

// hardware defines
// LEDs
#define USER_LED          15   // GPIO pin for heartbeat LED
#define LED_TIMEOUT       250  //Heartbeat LED cycle time in ms
#define FLICKER_TIMEOUT   66  //Firebox LED cycle time in ms
// H-bridge control outputs
#define IN1        18
#define IN2        20
// Firebox LED outputs
#define LED_R      17
#define LED_Y      19
// VBUS input (digital)
#define VBUS        1
// VBAT input (analogue)
#define VBAT        0
// expansion connector GPIO
#define EXT_GPIO   16

#include <loco_profiles.h> // build configs and specific loco profiles for motor control etc

#define DEBUG        0 // 0 = no debug

int8_t rxPower[4] = {0,0,0,0};   // (power for the selected loco in the UI), loco1, loco2, loco3
int8_t txStatus[4] = {0,0,0,0};   // LOCO_ID, spare, spare, vbat as % plus charging state

// motor
int power = 0;
int motor_power = 0;
int old_speed = 0;
float nudge = 0.0;

//LEDs
int lastFlickerTime = 0;
int lastLedTime = 0;
int ledState = 0;

int vbat = 0;

// handheld control MAC address
extern uint8_t targetAdress[] = {0xD0, 0xCF, 0x13, 0x1E, 0x12, 0x50}; // control unit address

esp_now_peer_info_t peerInfo;

// callback when data is sent
void OnDataSent(const uint8_t *mac_addr, esp_now_send_status_t status) {
  Serial.print("\r\nLast Packet Send Status:\t");
  Serial.println(status == ESP_NOW_SEND_SUCCESS ? "Delivery Success" : "Delivery Fail");
}


// callback for ESP-NOW packet Rx
void OnDataRecv(const uint8_t * mac, const uint8_t *incomingData, int len) {
  memcpy(&rxPower, incomingData, sizeof(rxPower)); // copy the 4 bytes we use
}

void setup() {
  Serial.begin(115200);
  Serial.println("startup");

   WiFi.mode(WIFI_STA);

  // Init ESP-NOW
  if (esp_now_init() != ESP_OK) {
    Serial.println("Error initializing ESP-NOW");
    return;
  }
  esp_now_register_recv_cb(esp_now_recv_cb_t(OnDataRecv));

  esp_now_register_send_cb(esp_now_send_cb_t(OnDataSent)); // cast to fix ESP_NOW API change 
  memcpy(peerInfo.peer_addr, targetAdress, 6);
  peerInfo.channel = 0;  
  peerInfo.encrypt = false;

  // Add peer        
  if (esp_now_add_peer(&peerInfo) != ESP_OK){
    Serial.println("Failed to add peer");
    return;
  }
  
 // Set motor connections as outputs
  pinMode(IN1, OUTPUT);
  pinMode(IN2, OUTPUT);

// set up PWM
  ledcAttach(IN1, PWM_FREQ, PWM_BITS);
  ledcAttach(IN2, PWM_FREQ, PWM_BITS);
 
// Stop motor (Hi-Z)
  digitalWrite(IN1, LOW);
  digitalWrite(IN2, LOW);

// set up on board 'heartbeat' LED
  pinMode(USER_LED, OUTPUT);
  ledcAttach(USER_LED, PWM_FREQ, PWM_BITS);  

#ifdef FIREBOX_LEDS
// set up firebox LEDs
  pinMode(LED_Y,    OUTPUT);
  pinMode(LED_R,    OUTPUT);
  ledcAttach(LED_Y,    PWM_FREQ, PWM_BITS);  
  ledcAttach(LED_R,    PWM_FREQ, PWM_BITS);

// firebox LEDs are initially off (1 = off)
  ledcWrite(LED_Y, 255);
  ledcWrite(LED_R, 255);
#endif

// 'charge' detection is by sensing VBUS 
  pinMode(VBUS, INPUT);

}

void loop() {

// it's alive! LED
  if ((millis() - lastLedTime) > LED_TIMEOUT) {
 
    lastLedTime = millis();

    if (ledState == 0) {

      ledcWrite(USER_LED, 255);
      ledState++;

    } else { 

      ledcWrite(USER_LED, 0);
      ledState--;

  // read battery voltage (average over 16 readings)
      vbat = 0;
      for (int i=0; i<16; i++) {
        vbat += (analogReadMilliVolts(VBAT) * 2); // VBAT input is via a 2:1 resistive divider
      }
      vbat /= 16;

// build status packet      
      txStatus[3] = map(vbat, 3000, 4200, 0, 100); //3.00V->4.2V maps to 0->100%
      if (digitalRead(VBUS)) {
        txStatus[3] |= 0x80; // set msb if charging
      }
      txStatus[0] = LOCO_ID;

// send the status packet
esp_err_t result = esp_now_send(targetAdress, (uint8_t *) &txStatus, sizeof(txStatus));

    }
  }

#ifdef FIREBOX_LEDS
  if ((millis() - lastFlickerTime) > FLICKER_TIMEOUT) {
 
    lastFlickerTime = millis();

// FIXME - this needs to be tied to actual charging rather than bus power present
    if (digitalRead(VBUS)) {             // only illuminate firebox if charging
      ledcWrite(LED_R, 255-(random(180)+75));
      ledcWrite(LED_Y, 255-(random(90)+65));
    } else {                            //LEDs off
      ledcWrite(LED_Y, 255);
      ledcWrite(LED_R, 255);
    }
  } 
# endif

// calculate motor power and set PWM channel according to direction
  power = (int)abs(rxPower[LOCO_ID]); // note cast from CHAR to INT

  if (abs(rxPower[LOCO_ID]) == rxPower[LOCO_ID]) { // -ve values are reverse
  
    motor_power = map(power, 0, 100, FWD_DEAD_BAND, MAX_POWER);
  
    if ((old_speed == 0) && power != 0) {  // 'nudge' motor on start
      nudge = INITIAL_NUDGE;
    }
    motor_power += int(nudge);
    motor_power = (motor_power < 0) ? 0 : motor_power; //clamp motor_power
    motor_power = (motor_power > MAX_POWER) ? MAX_POWER : motor_power;
    
    nudge -= NUDGE_DECAY;
    nudge = (nudge < 0.0) ? 0.0 : nudge;

    motor_power = (motor_power <= FWD_DEAD_BAND) ? 0 : motor_power; // force a stop at DEAD_BAND value

    ledcWrite(IN1, 0);
    ledcWrite(IN2, motor_power);

  } else {
  
    motor_power = map(power, 0, 100, REV_DEAD_BAND, MAX_POWER);
  
    if ((old_speed == 0) && power != 0) {  // 'nudge' motor on start
      nudge = INITIAL_NUDGE;
    }
        motor_power += int(nudge);
    motor_power = (motor_power < 0) ? 0 : motor_power; //clamp motor_power
    motor_power = (motor_power > MAX_POWER) ? MAX_POWER : motor_power;
    
    nudge -= NUDGE_DECAY;
    nudge = (nudge < 0.0) ? 0.0 : nudge;

    motor_power = (motor_power <= REV_DEAD_BAND) ? 0 : motor_power; // force a stop at DEAD_BAND value

    ledcWrite(IN2, 0);
    ledcWrite(IN1, motor_power);

  }
  
  old_speed = power;

  if (DEBUG) {
  Serial.print("power = ");
  Serial.print(power, DEC);
  Serial.print("   motor_power = ");
  Serial.print(motor_power, DEC);
  Serial.print("   nudge = ");
  Serial.print(nudge, DEC);
  Serial.print("   old_speed = ");
  Serial.println(old_speed, DEC);
  }

//delay(1);

}

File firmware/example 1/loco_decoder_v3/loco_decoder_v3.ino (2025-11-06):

//
// Simple POC for control of locomotive
//  based on esp32-web-server-websocket-sliders example from
// Rui Santos & Sara Santos - Random Nerd Tutorials
// 

// v3 - version for the Seed Studio XIAO ESP32C6based hardware

#include <Arduino.h>
#include <WiFi.h>
#include <ESPAsyncWebServer.h>
#include <AsyncTCP.h>
#include "LittleFS.h"
#include <Arduino_JSON.h>

// hardware defines
// LEDs
#define USER_LED          15   // GPIO pin for heartbeat LED
#define LED_TIMEOUT       250  //Heartbeat LED cycle time in ms
#define FLICKER_TIMEOUT   66  //Firebox LED cycle time in ms
// H-bridge control outputs
#define IN1        18
#define IN2        20
// Firebox LED outputs
#define LED_R      17
#define LED_Y      19
// VBUS input (digital)
#define VBUS        1
// VBAT input (analogue)
#define VBAT        0
// expansion connector GPIO
#define EXT_GPIO   16
 
// build configs
//#define DAPOL_B4       // build for Dapol B4
#define DAPOL_58XX     // build for Dapol 58XX
//#define PRM_14XX       // build for PRM 14XX
//#define PRM_PANNIER    // build for PRM 'Pannier'

#ifdef DAPOL_B4
// network credentials for AP
const char* ssid = "Dapol B4";
const char* password = "";
// filepath to root html in FLASH filesystem
const char* index_file = "/dapol_b4.html";
#define FIREBOX_LEDS 1   // red and yellow LEDs in firebox
// motor defines
#define DAPOL 1       // buil for Dapol 0 gauge 5 pole motor
#define DEAD_BAND 130
// PWM init
#define PWM_BITS 8
#define PWM_FREQ 10000
// physics defines
#define FRICTION 1
#endif

#ifdef DAPOL_58XX
// network credentials for AP
const char* ssid = "LocoController";
const char* password = "";
// filepath to root html in FLASH filesystem
const char* index_file = "/dapol_58xx.html";
#define FIREBOX_LEDS 1   // red and yellow LEDs in firebox
// motor defines
#define DAPOL 1       // build for Dapol 0 gauge 5 pole motor
#define DEAD_BAND 120
// PWM init
#define PWM_BITS 8
#define PWM_FREQ 10000
// physics defines
#define FRICTION 1
#endif

#ifdef PRM_14XX
// network credentials for AP
const char* ssid = "PRM 14XX";
const char* password = "";
// filepath to root html in FLASH filesystem
const char* index_file = "/prm_14xx.html";
#define FIREBOX_LEDS 0   // no firebox LEDS
// motor defines
#define N20         1  // build for N20 motor and gearbox
#define DEAD_BAND 100
// PWM init
#define PWM_BITS 8
#define PWM_FREQ 5000
// physics defines
#define FRICTION 1
#endif

#ifdef PRM_PANNIER
// network credentials for AP
const char* ssid = "PRM Pannier";
const char* password = "";
// filepath to root html in FLASH filesystem
const char* index_file = "/prm_pannier.html";
#define FIREBOX_LEDS 0   // no firebox LEDS
// motor defines
#define N20         1  // build for N20 motor and gearbox
#define DEAD_BAND 100
// PWM init
#define PWM_BITS 8
#define PWM_FREQ 5000
// physics defines
#define FRICTION 1
#endif

#define DEBUG        1 // 0 = no debug
#define ACCESS_POINT 1 // 1 = use internal access point, 0 = use external network

// Create AsyncWebServer object on port 80
AsyncWebServer server(80);
// Create a WebSocket object
AsyncWebSocket ws("/ws");

String message = "";
String sliderValue1 = "0";
String sliderValue2 = "0";
String sliderValue3 = "0";
String chargeState = " ";

int power = 0;
int motor_power = 0;
int throttle = 0;
int reverser = 0;
int brake = 100;

int lastFlickerTime = 0;
int lastLedTime = 0;
int ledState = 0;
int vbat = 0;

//Json Variable to Hold values
JSONVar sliderValues;

//Get Slider Values
String getSliderValues(){
  sliderValues["sliderValue1"] = sliderValue1;
  sliderValues["sliderValue2"] = sliderValue2;
  sliderValues["sliderValue3"] = sliderValue3;
  sliderValues["power"] = String(power);

  if (digitalRead(VBUS)) {             // add charging state to VBAT reading
  chargeState = "(charging)  "+String(float(vbat)/1000);
  sliderValues["batteryvolts"] = chargeState;
  } else {
    sliderValues["batteryvolts"] = String(float(vbat)/1000);
  }
    
  String jsonString = JSON.stringify(sliderValues);

  if (DEBUG) {
    Serial.println(jsonString);
  }
  return jsonString;}

// Initialize LittleFS
void initFS() {
  if (!LittleFS.begin()) {
    Serial.println("An error has occurred while mounting LittleFS");
  }
  else{
   Serial.println("LittleFS mounted successfully");
  }
}

// Initialize WiFi
void initWiFi() {

  if (ACCESS_POINT) { // use internal access point
    
    Serial.print("Setting AP (Access Point)…");
    WiFi.softAP(ssid /*, password*/);   // password parameter removed for open access

    IPAddress IP = WiFi.softAPIP();
    Serial.print("AP IP address: ");
    Serial.println(IP);
    
  } else { // use external network
      
    WiFi.mode(WIFI_STA);
    WiFi.begin(ssid, password);
    Serial.print("Connecting to WiFi ..");

    while (WiFi.status() != WL_CONNECTED) {
      Serial.print('.');
      delay(1000);
      }

    Serial.println(WiFi.localIP());
  }
}


void notifyClients(String sliderValues) {
  ws.textAll(sliderValues);
}

void handleWebSocketMessage(void *arg, uint8_t *data, size_t len) {
  AwsFrameInfo *info = (AwsFrameInfo*)arg;
  if (info->final && info->index == 0 && info->len == len && info->opcode == WS_TEXT) {
    data[len] = 0;
    message = (char*)data;

    if (DEBUG) {
      Serial.print("message = ");     Serial.println(message);
    }

    if (message.indexOf("1s") >= 0) {
      sliderValue1 = message.substring(2);
      notifyClients(getSliderValues());
    }

    if (message.indexOf("2s") >= 0) {
      sliderValue2 = message.substring(2);
      notifyClients(getSliderValues());
    } 

    if (message.indexOf("3s") >= 0) {
      sliderValue3 = message.substring(2);
      notifyClients(getSliderValues());
    }
    if (strcmp((char*)data, "getValues") == 0) {
      notifyClients(getSliderValues());
    }
  }
}
void onEvent(AsyncWebSocket *server, AsyncWebSocketClient *client, AwsEventType type, void *arg, uint8_t *data, size_t len) {
  switch (type) {
    case WS_EVT_CONNECT:
      Serial.printf("WebSocket client #%u connected from %s\n", client->id(), client->remoteIP().toString().c_str());
      break;
    case WS_EVT_DISCONNECT:
      Serial.printf("WebSocket client #%u disconnected\n", client->id());
      break;
    case WS_EVT_DATA:
      handleWebSocketMessage(arg, data, len);
      break;
    case WS_EVT_PONG:
    case WS_EVT_ERROR:
      break;
  }
}

void initWebSocket() {
  ws.onEvent(onEvent);
  server.addHandler(&ws);
}

void setup() {
  Serial.begin(115200);
  Serial.println("startup...");

  initFS();
  initWiFi();

 // Set motor connections as outputs
  pinMode(IN1, OUTPUT);
  pinMode(IN2, OUTPUT);

// set up PWM
  ledcAttach(IN1, PWM_FREQ, PWM_BITS);
  ledcAttach(IN2, PWM_FREQ, PWM_BITS);
 
// Stop motor (Hi-Z)
  digitalWrite(IN1, LOW);
  digitalWrite(IN2, LOW);

  initWebSocket();
  
// Web Server Root URL
  server.on("/", HTTP_GET, [](AsyncWebServerRequest *request){
    request->send(LittleFS, index_file, "text/html");
  });
  
  server.serveStatic("/", LittleFS, "/");
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

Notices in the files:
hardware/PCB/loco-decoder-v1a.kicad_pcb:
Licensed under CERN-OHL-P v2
